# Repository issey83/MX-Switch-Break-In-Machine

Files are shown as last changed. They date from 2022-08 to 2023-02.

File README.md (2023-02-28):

# MX Switch Break-In Machine
A simple machine designed to actuate/ break-in MX style switches consistently and repetitively for a smoother push feel. Watch the [assembly process and operation](https://www.youtube.com/watch?v=iYIlCdo38ZM&list=PLLd9RKaLkD3lO_kQBJ3w394Xko4Nm3RR9) of the machine here.



[snapshot]: /Images/DSC05789.jpg "Machine Snapshot"

## Specifications
- Max number of switches: 36
- Compatibility: 
  -  MX style switches with total travel distance of 4mm
  -  MX style switches with total travel distance less than 4mm (tweaks required for this)

## Notes ⚠️
- The provided files are to be used at your own risk.
- The dimensional tolerances may vary between 3D printers. See acceptable tolerances under [`Production/Technical-Drawings`](/Production/Technical-Drawings).
- The complete units showed in pictures and videos shared in this repo were printed with [JLCPCB 3D printing service](https://cart.jlcpcb.com/quote), with material of 8000 Resin, and remarked to print at an 30/45 angle for better Z-axis accuracy.
- Do ensure to run the machine at a ventilated area or fan-cooled to prevent the motor from overheating.

## Bill of materials (BOM) 📜
The following is the number of quantities required for each part to assemble a complete unit. The part files required to print are under the [`Production`](/Production) folder.

Parts required to print:
| Part | Qty | Comment |
| --- | --- | --- |
| Actuation Plate | 2 | - |
| Off Center Actuation Plate | 4 | - |
| Switch Holder | 4 | - |
| Flat Profile Keycap *or 10xFlat Profile Keycap* | 36 *or 4*  | - |
| Machine Housing | 1 | - |
| Machine Housing 1 *or 4xMachine Housing 1* | 2 *or 1* | - |
| Motor-Adjuster | 1 | - |
| Scotch Yoke | 1 | - |

Parts required to purchase:
| Part | Qty | Comment | References |
| --- | --- | --- | --- |
| TT 1:90 Gearbox DC Motor | 1 | Measured about 155 actutations/min, 5.4 hours for 50k actuations (measurement based on my purchased motor) | [link 1](https://shopee.sg/Large-Price-Metal-Gear-Robot-Smart-Car-Reduce-Speed-Motor-Tt-Motor-i.191993938.3917622642) |
| *or TT 1:48 Gearbox DC Motor* | 1 | Motor runs hot over long run, measured about 400 actutations/min, 2.1 hours for 50k actuations (measurement based on my purchased motor) | [link 2](https://www.adafruit.com/product/3777) |
| HK 0306 Needle Roller Bearing | 2 | - | [link 1](https://www.skf.com/us/products/rolling-bearings/roller-bearings/needle-roller-bearings/drawn-cup-needle-roller-bearings/productid-HK%200306%20TN) |
| M3 x 8mm Screw | 6 | - | - |
| M3 x 12mm Screw | 2 | - | - |
| M3 x 25mm Screw | 2 | - | - |
| Female USB C to 2-pin 22 AWG Wires | 1 | - | [link 1](https://www.aliexpress.com/item/1005001388133794.html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) <br> [link 2](https://www.aliexpress.com/item/1005002271810476.html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) |
| 8mm Diameter Bumpons | 4 | Optional | [link 1](https://shopee.sg/MAGIC-100PCS-Sheet-Soft-Buffer-Sticker-Furniture-Accessories-Gel-Shock-Absorber-Rubber-Silicone-Pads-Cabinets-Door-Stop-Anti-collision-Toilets-Bump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) |

## To-Do 📝
- A guide on breaking-in switches that have shorter travel distance will be shared soon.

## Changelog 📒
- `05/02/2022:` Initial part files commit 

## Reach me at 📩
- Discord: https://discordapp.com/users/Yū#0001
  - Feel free to send me your enquires if you have doubt reproducing a unit for yourself.

---------------------------------------------------------------------------------------------------------
# FDM Printed, with modifications
Replaceable fan/motor without soldering, to be used with 12v power supply, or USB QC/PD trigger module for 12v output.

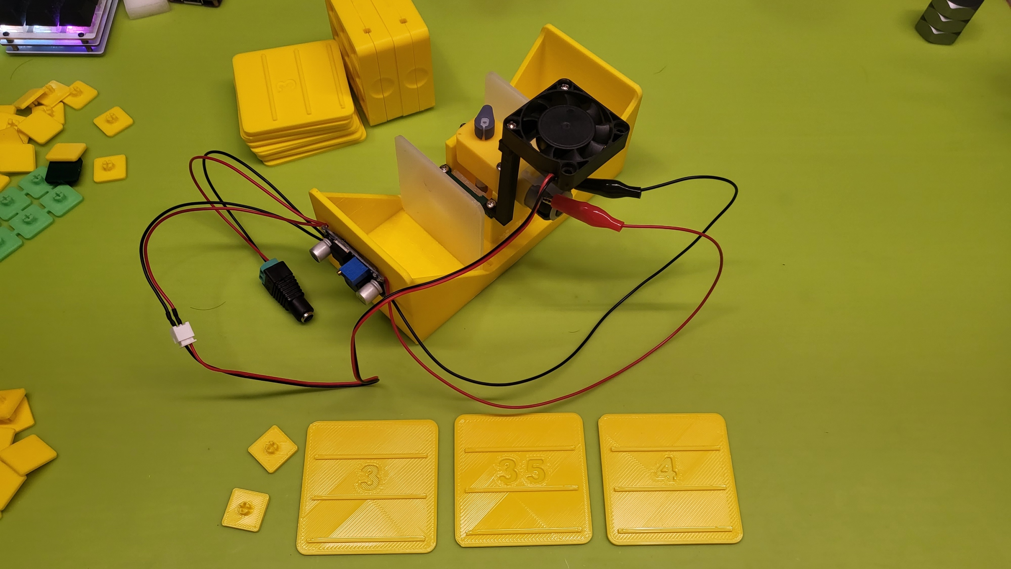
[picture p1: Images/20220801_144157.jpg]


[snapshot2]: /Images/20220801_144157.jpg "FDM Printed, with fan." 

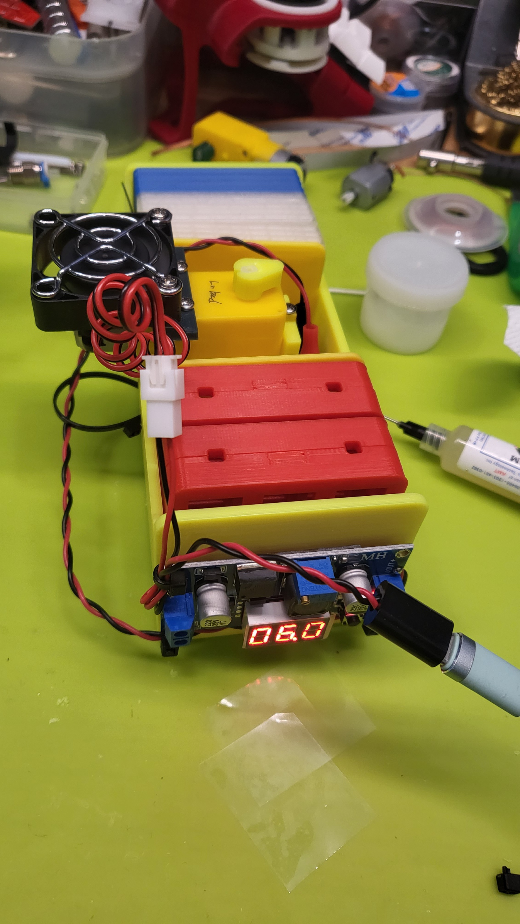
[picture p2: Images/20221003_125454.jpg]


[snapshot3]: /Images/20221003_125454.jpg "PD/QC trigger, LM2596 with display, new fan mount" 

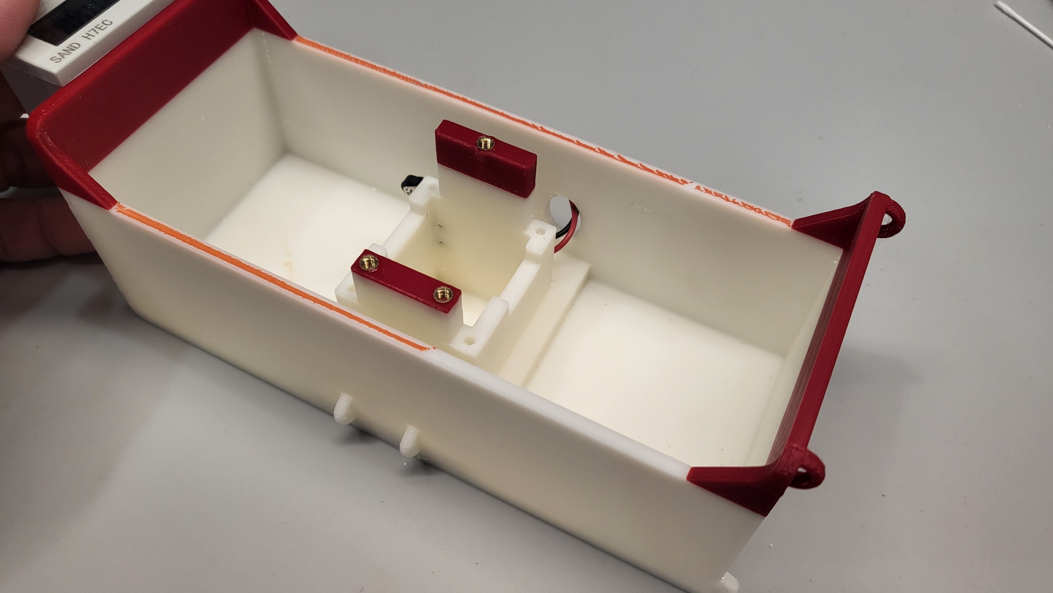
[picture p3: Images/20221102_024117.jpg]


[snapshot4]: /Images/20221102_024117.jpg "Main housing with brass inserts, cable tie points." 

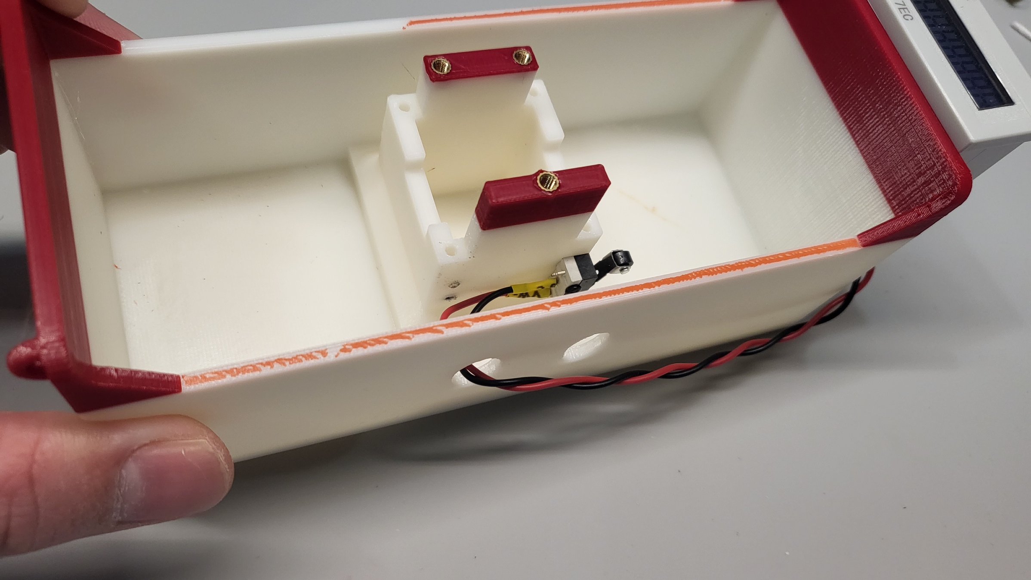
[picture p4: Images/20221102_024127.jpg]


[snapshot5]: /Images/20221102_024127.jpg "Micro switch location, access hole." 

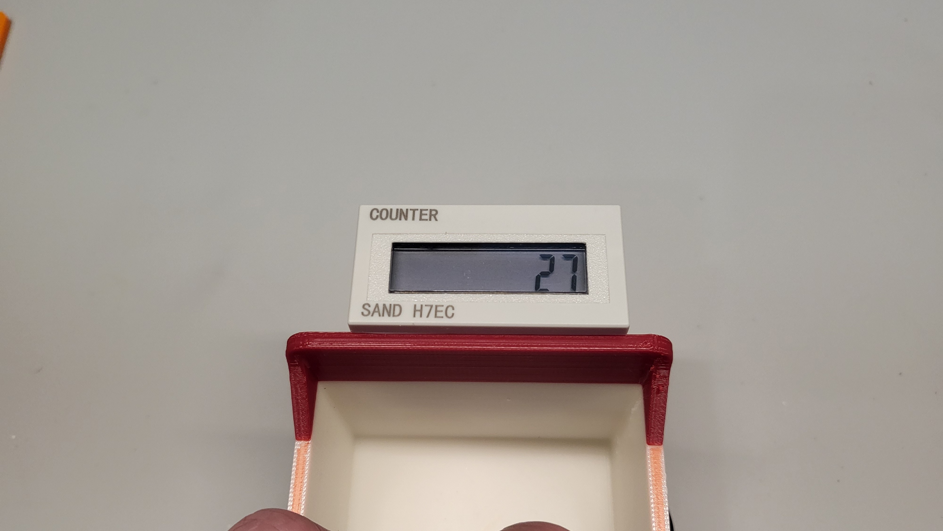
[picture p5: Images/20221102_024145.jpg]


[snapshot6]: /Images/20221102_024145.jpg "8 digit counter." 

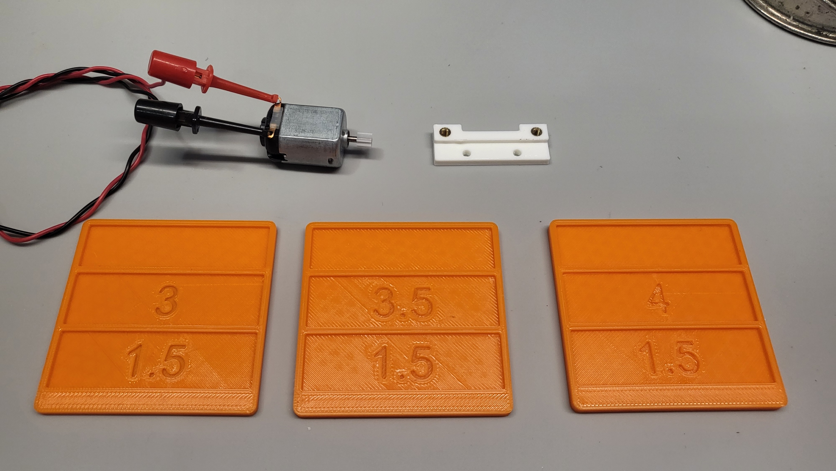
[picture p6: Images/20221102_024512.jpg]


[snapshot7]: /Images/20221102_024512.jpg "Off center plate, with borders, fan mount with brass inserts, 42mm test hook." 

## Utilizing 
- QC/PD trigger module for 12v input, because QC/PD power brick better than regular usb port/charger
- LM2596 power supply module for voltage control, controling motor speed
- 12v 40x10mm fan, should be easy to source, and normally they come in XH connector
- XH 2.54 2pin header for fan
- 28mm aligator clips / 42mm test hook
- M3 x 4mm or M3 x 4.5mm brass inserts for frequent change of gearbox/motor assembly
- 8 digit counter found on taobao, https://item.taobao.com/item.htm?id=547288386556, I use H7EC-BLM, no need external power, battery last for 3-5 years according to description. 
- some soldering work
you can make this end user friendly, changing parts without soldering.

Changes made to STL files for 3d FDM printing.
1. Added marking to off center actuation plate, 3/3.5/4mm version. Mix and match to use with different switch's total travel, also to offset some printing errors, if any.
1.1. Added borders on off center plate, to prevent plate to press into main housing and causing arch.
2. Added fan mount, can be used with m3 x 8mm screw (might strip easy), or use with m3 x 12mm screw for a better hold. Screw length for the fan will depend on thickness of the fan you are getting, and if there's fan guard. for 10mm thick, I use m3 x 16mm.
2.1 New fan mount design, closer to motor, using motor's mounting screw, less material needed for printing. Brass insert optional, files provided.
3. Added keycap file for FDM printing, more tolerance, fit better. Can be used with dustproof stem as well. Closed off part is for east/west side of the stem, opening side face north/south, north/south is the leaf/led side of the switch.
4. New addition to main housing, some rings for cable management, soldered joint on wire is brittle, might break if they are moved frequent, tie them down. Also some place for fixing a micro switch, I think I got the right side position correct for a micro switch with lever + wheel attached, left side might not be. Use size M2 screw for holding the switch.

How I build and run them.
1. Ironing enabled for main housing, making sure the floor is flatter than regular printed parts.
2. Brass inserts, 3x4mm or 3x4.5mm, depth don't really matter, 3-4mm is fine.
3. Scotch yoke printed in nylon, actuation plate printed in ABS, fan mount printed in nylon/ABS.
4. Lubricate the floor of main housing, neck of actuation plate, scotch yoke with sw92sa from aliexpress, or any kind of lube for plastic (205g0 works too, expensive).
5. Lubricate internals of gearbox with PTFE dry lube from WD-40, or any spray lube for plastic.

# JGA25-370 motor housing, mounting, scotch yoke update
Using a more powerful motor, this should be able to run 36x cherry hg black 80g easy, and require a lot less motor replacement (TT motors)
Updated: Main housing, actuation plate housing lock, motor mounting plate, scotch yoke, bearing
Retained: Switch carriage, actuation plate, off center actuation plate, flat profile keycaps

Parts list to purchase:

1. JGA25-370 - https://item.taobao.com/item.htm?id=691467377622
I'm using 12v 282rpm myself, with voltage control, 200rpm to 300rpm, translate to 400-600 actuations per minute, 576k to 864k actuations per 24 hour.
12v 169rpm and 282rpm should work fine, I'm not sure about 6v, you should test this yourself if you want to run it with direct usb power.

2. Small bearing with screw embedded - https://item.taobao.com/item.htm?id=672727759613
JS6837-3C1L6M3
I've found that the previous bearing choice has a bit too much wobble/free-play, and if fastened tight, the bearing won't spin, if not fastened tight, screw may dislodge over time. This new one allows tightening and a lot less free-play, less maintenance.

Special durable material choice:
Nylon: actuation plate, scotch yoke, they last very long compared to PLA and ABS. Haven't tried PETG yet, YMMV.
High temperature resistant material: motor mounting plate. It might get hot, just in case.
Everything else can be printed in cheap PLA, and last quite some time.

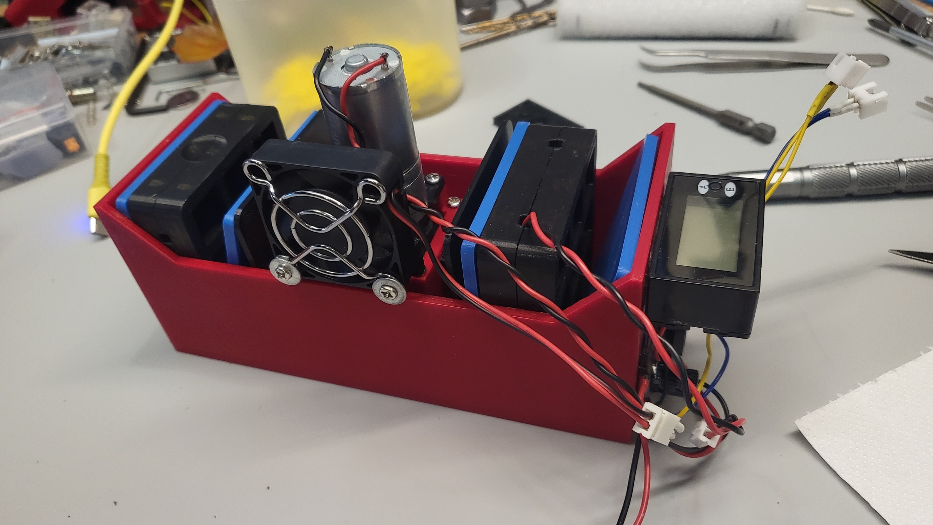
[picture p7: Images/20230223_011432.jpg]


[snapshot8]: /Images/20230223_011432.jpg "My setup/config, with fan, voltage control, double 8 digit counter." 

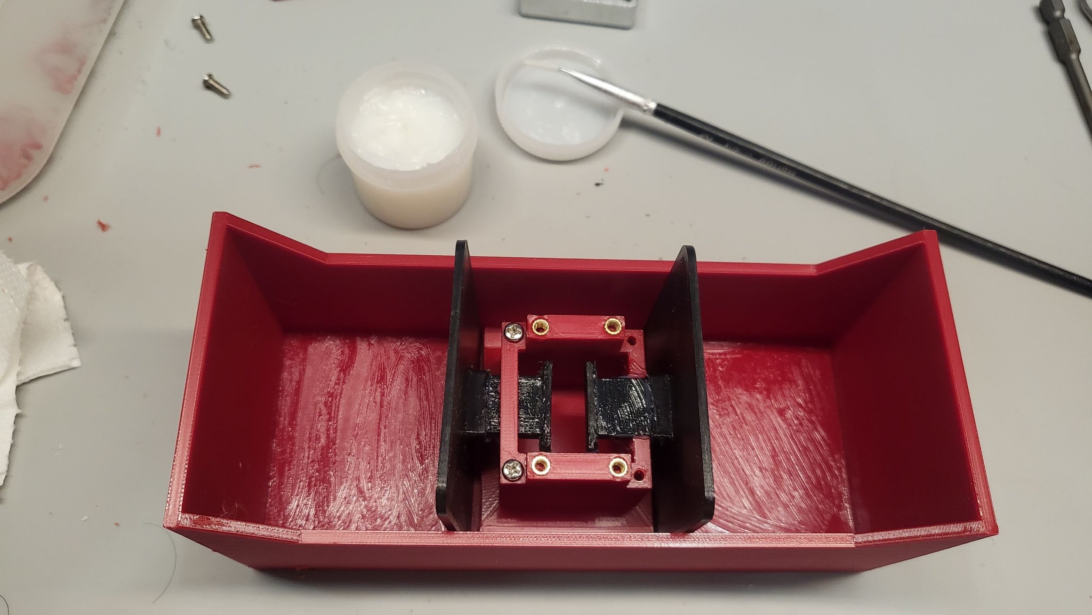
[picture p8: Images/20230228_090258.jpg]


[snapshot9]: /Images/20230228_090258.jpg "Cheap SW-92SA lube." 

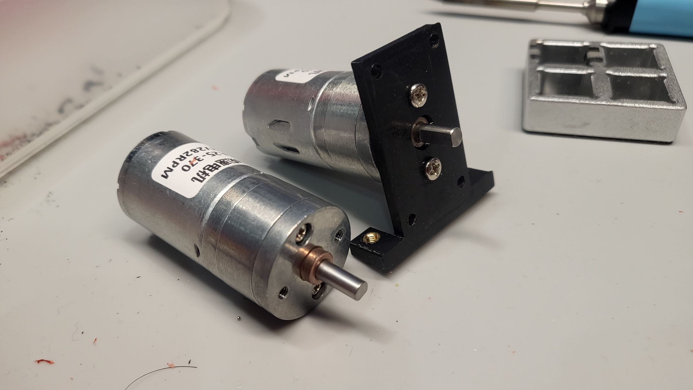
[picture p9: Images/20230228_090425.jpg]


[snapshot10]: /Images/20230228_090425.jpg "JGA25-370." 

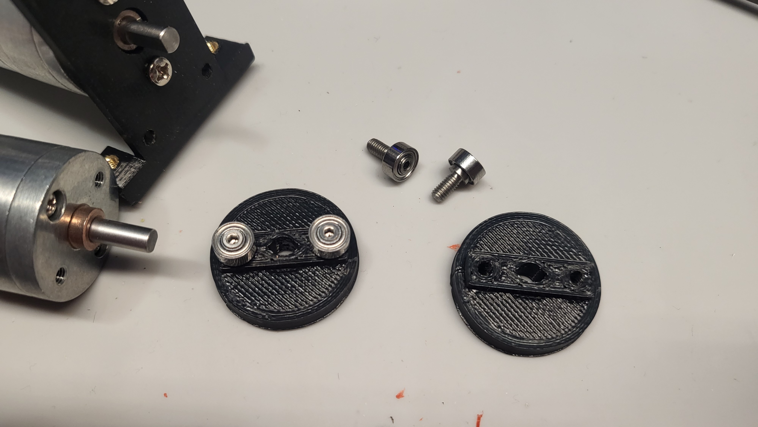
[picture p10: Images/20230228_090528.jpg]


[snapshot11]: /Images/20230228_090528.jpg "New scotch yoke and bearings." 

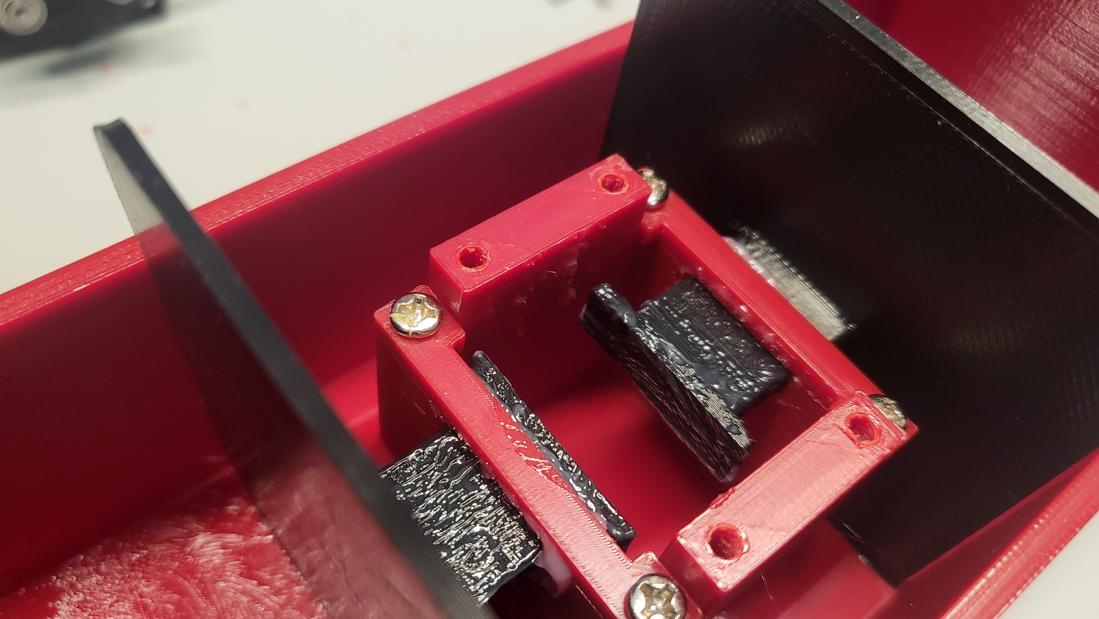
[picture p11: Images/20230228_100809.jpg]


[snapshot12]: /Images/20230228_100809.jpg "Lube between actuation plate and scotch yoke." 

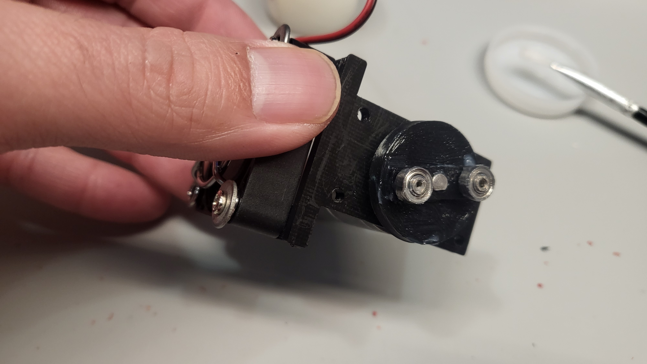
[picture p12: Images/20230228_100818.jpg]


[snapshot13]: /Images/20230228_100818.jpg "Scotch yoke should sit flush with motor shaft." 

Good luck and have fun building.

You can reach me through discord
issey83's corner - https://discord.gg/jTNPmTvsRC

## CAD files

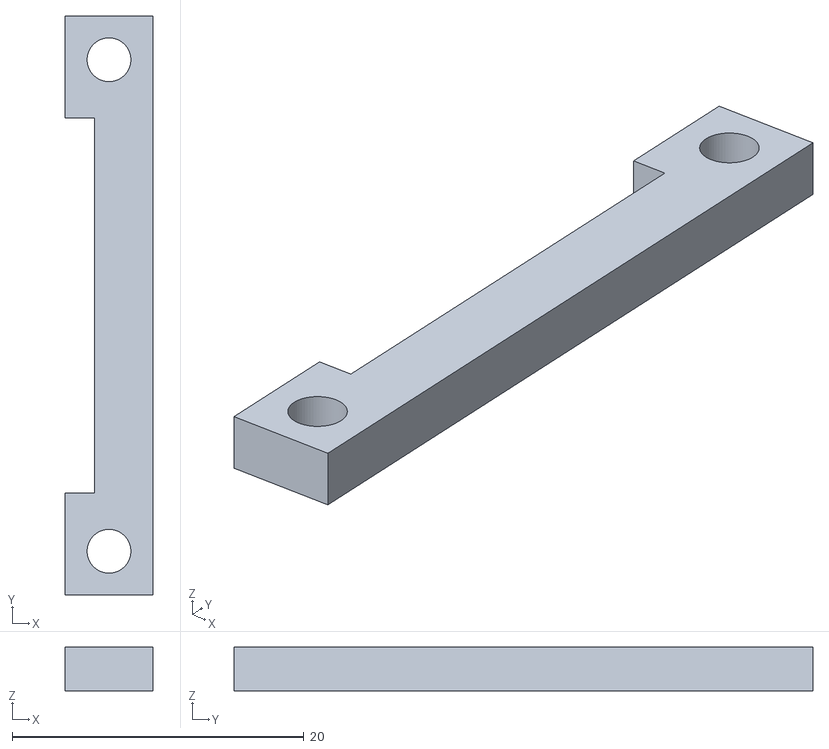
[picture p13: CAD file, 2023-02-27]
Production/STL/jga25/jga housing plate lock.stl
6.00 x 39.7 x 3.00

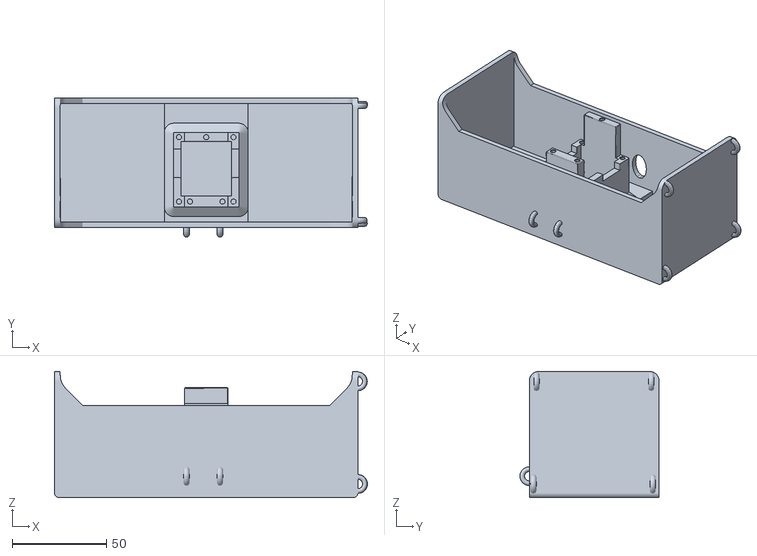
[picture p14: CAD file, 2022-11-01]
Production/STL/v2/machine housing v4.stl
166.3 x 74.0 x 67.0

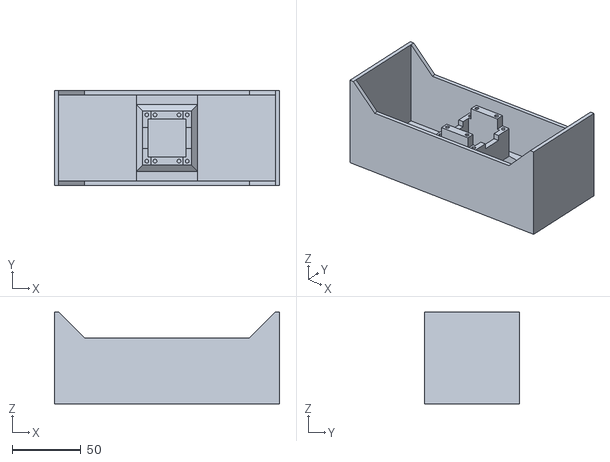
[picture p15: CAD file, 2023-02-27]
Production/STL/jga25/jga25 housing v2.stl
164.1 x 69.0 x 67.0

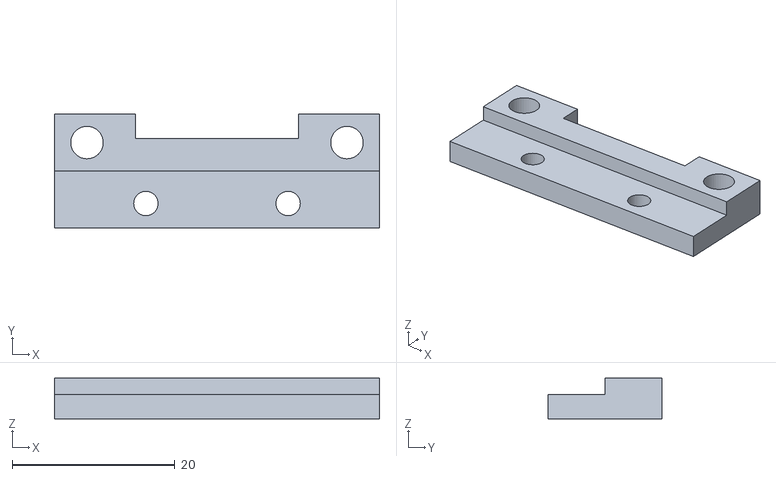
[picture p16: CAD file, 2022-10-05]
Production/STL/v2/fan mount v3.stl
40.0 x 14.0 x 5.00

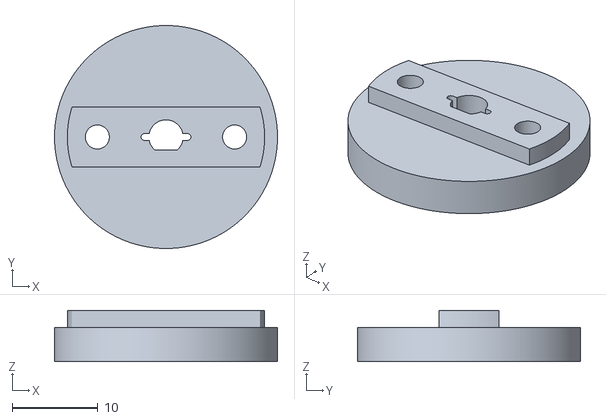
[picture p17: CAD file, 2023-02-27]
Production/STL/jga25/jga25 scotch yoke.stl
26.0 x 26.0 x 6.00

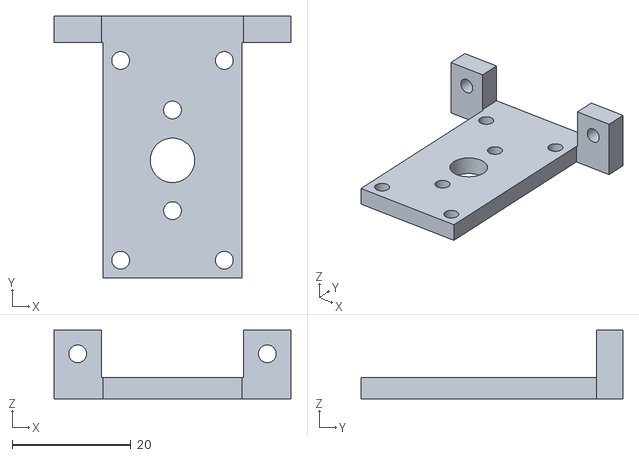
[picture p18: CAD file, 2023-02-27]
Production/STL/jga25/jga25 mounting plate fan 3mm.stl
40.0 x 44.2 x 11.6

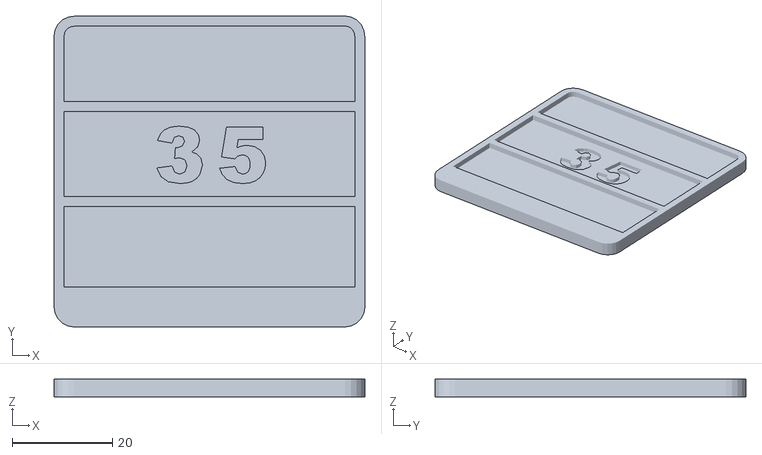
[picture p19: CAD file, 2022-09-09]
Production/STL/v2/off center plate 1.5mmx3.5mm.stl
62.0 x 62.0 x 3.50

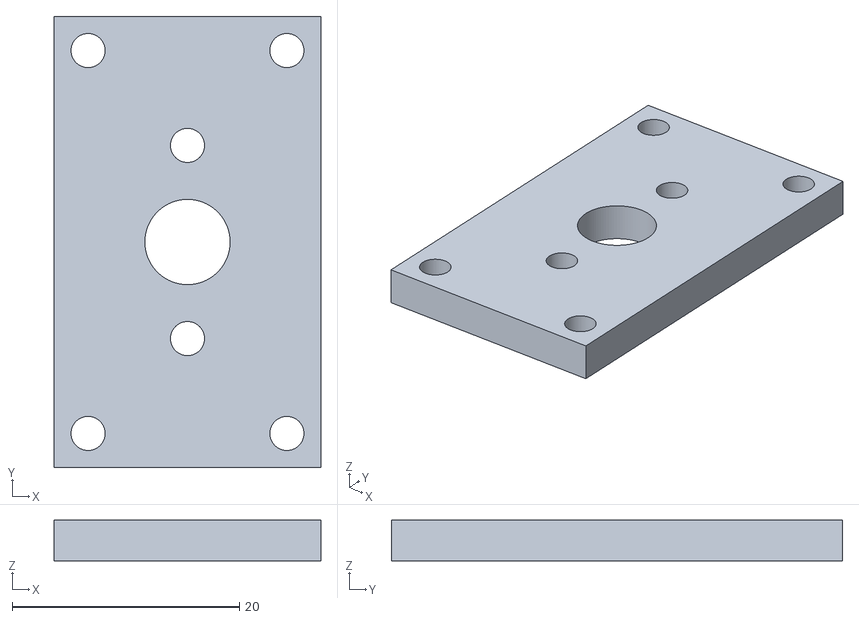
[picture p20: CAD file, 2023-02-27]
Production/STL/jga25/jga25 mounting plate.stl
23.5 x 39.7 x 3.60

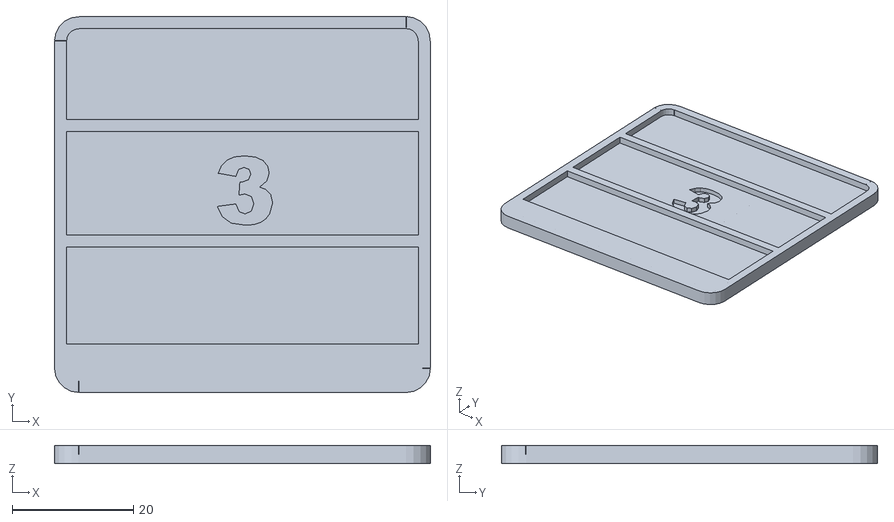
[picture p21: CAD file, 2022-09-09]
Production/STL/v2/off center plate 1.5mmx3mm.stl
62.0 x 62.0 x 3.00

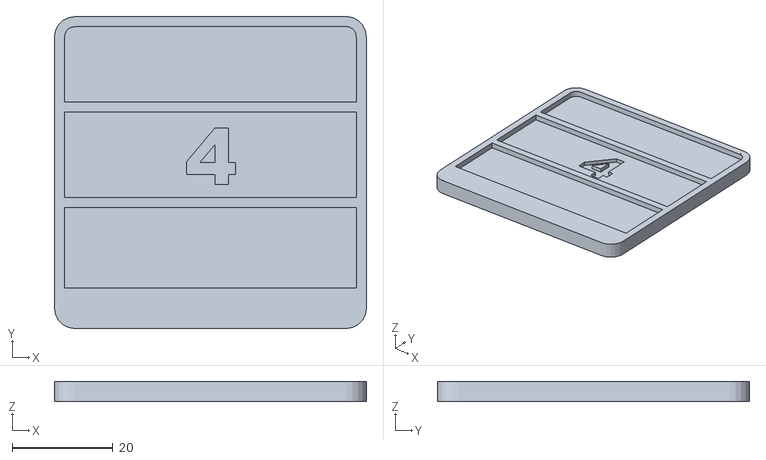
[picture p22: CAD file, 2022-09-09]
Production/STL/v2/off center plate 1.5mmx4mm.stl
62.0 x 62.0 x 4.00

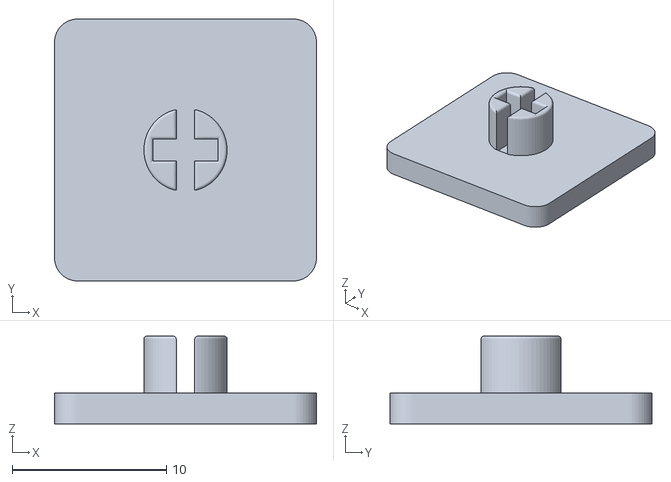
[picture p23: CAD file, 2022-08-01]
Production/STL/v2/FDM Flat keycap.stl
17.0 x 17.0 x 5.70

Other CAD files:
Production/STL/v2/machine housing v3.stl
